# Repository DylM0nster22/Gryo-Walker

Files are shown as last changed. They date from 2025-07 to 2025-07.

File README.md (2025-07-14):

# Torque Walker
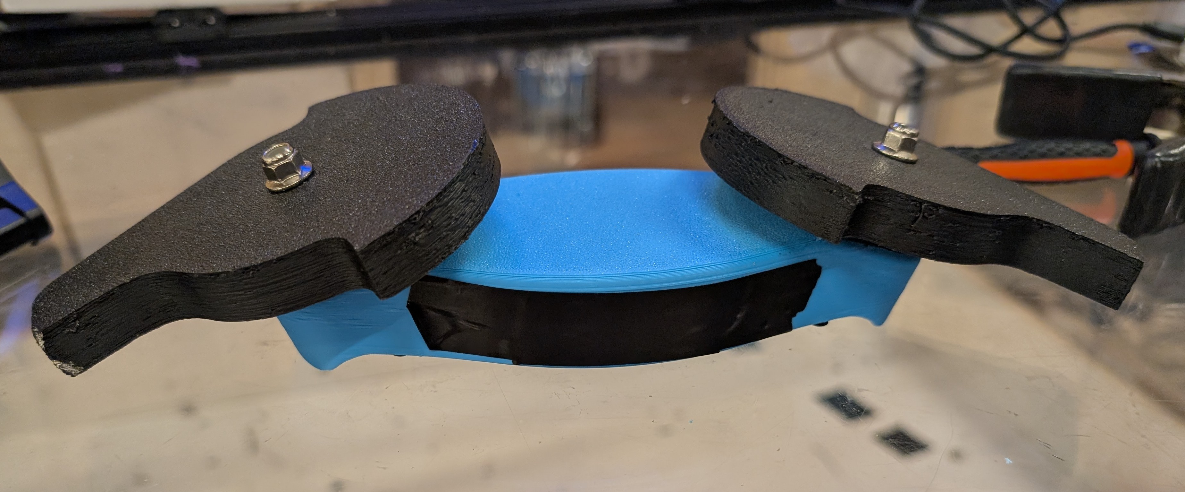
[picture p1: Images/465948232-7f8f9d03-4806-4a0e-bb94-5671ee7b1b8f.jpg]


# [DEMO VIDEO](https://photos.app.goo.gl/9bNn2mUH8ifmHqGP9)

## Background

For our project for Undercity, we made a torque walker combat robot. This style of robot has two diagonally spinning blades, with one on each side of the robot. The blades rotate in opposite directions. By adjusting the speed of each blade, the torque reaction causes the robot to pivot, which can be used to create a walking motion. 

The blades and frame were all printed from PLA. The robot has two RS2205 motors, one per weapon, which are held on with M3 x 8mm screws. These motors are drived by LanRC 35A ESCs, which are in turn powered by a 300mah Gaoneng LiHV 3S battery. The robot is powered on and off thorugh a fingertech switch, with the switch located in the bottom of the robot. We used a Malenki HV as our receiver, as it is what we had on hand. All of the electronics are held in by the bottom plate, which was held on with 4 M3 plastites. 

## Features

* Two large 5" diameter asymmetric disk weapons
* Tip speed exceeding 300 mph
* 3S 300mah High Voltage LiPo
* Able to be built with only off the shelf parts and 3D prints.

## Images

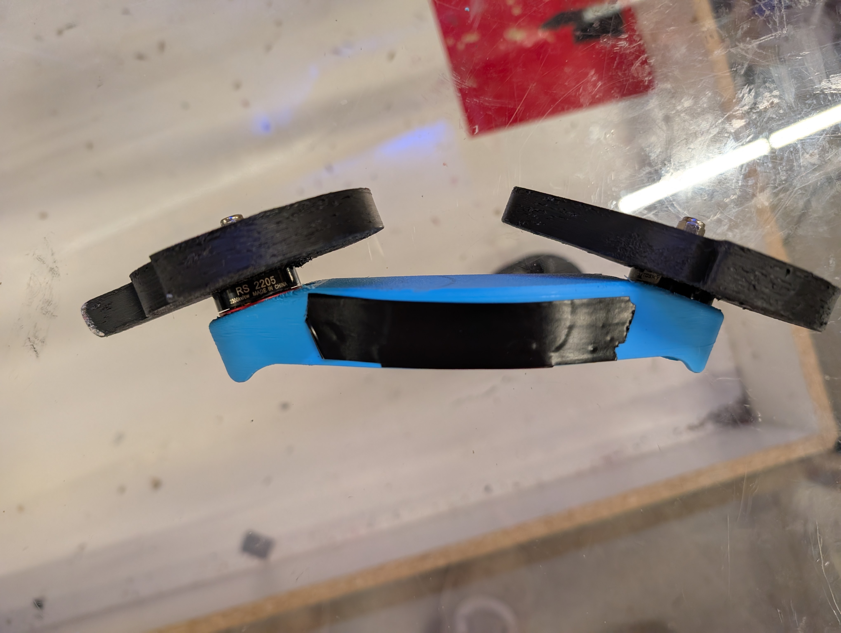
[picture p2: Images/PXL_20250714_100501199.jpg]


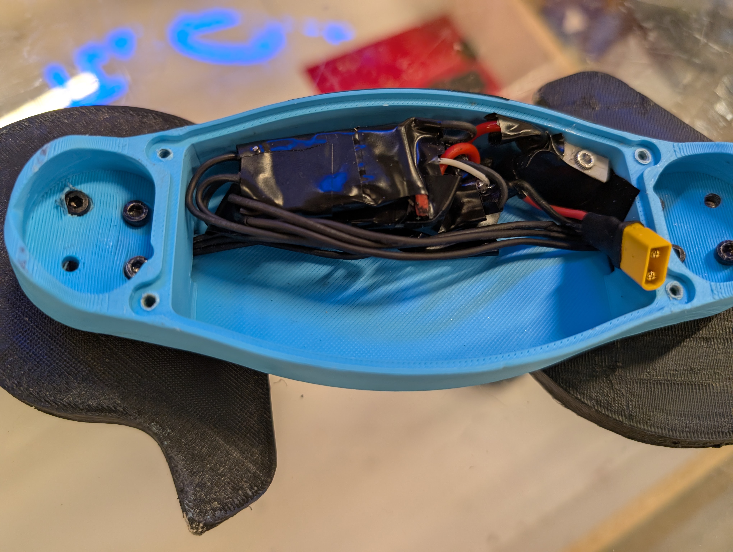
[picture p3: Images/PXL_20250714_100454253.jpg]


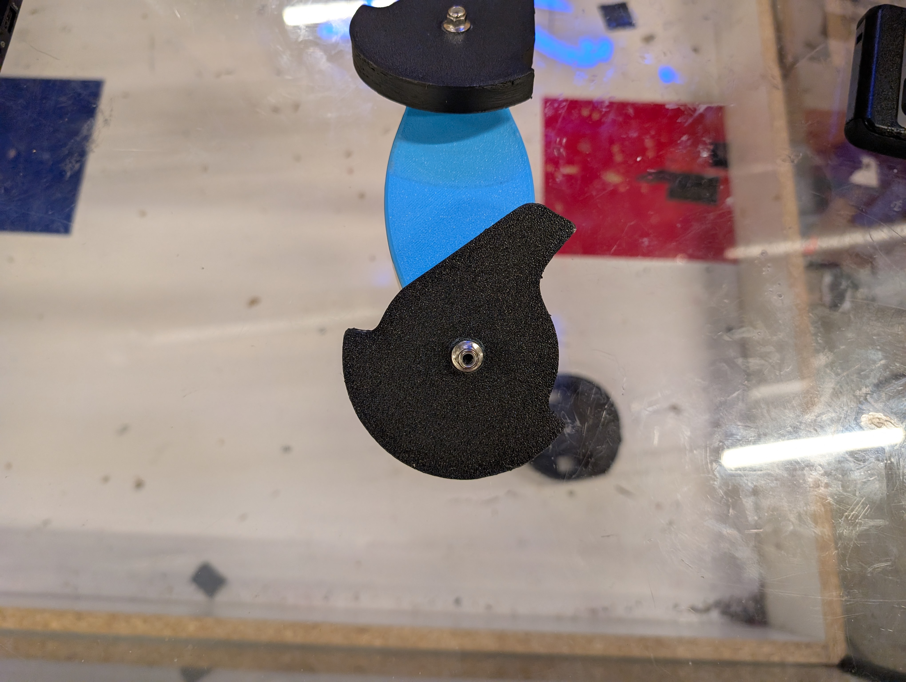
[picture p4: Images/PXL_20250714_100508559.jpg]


## Build Process

### Printing

**IT IS VERY IMPORTANT THAT WHEN PRINTING THE WEAPONS, ONE OF THE WEAPONS NEEDS TO BE MIRRORED.**

To begin the build process, first print all of the parts out of PLA. The robot is compact enough to be underweight for the plastic antweight class with almost any print settings, but the recommended settings are at least 4 walls 15% infil for the frame and all top layers (solid) for the weapons. This ensures that the robot is capable of holding up to the forces of combat.

### Electrical

The first step in the electrical system is to take a male XT30 and solder a black wire onto the negative side, and a red wire to the positive side (matching the battey). Solder the negative wire onto the negative terminal of the Malenki, and the positive wire onto one of the switch's tabs. Then solder another red wire onto the other tab of the switch, and then the other side of the wire can then be soldered onto the Malenki's positive terminal. 

Next, solder white signal wires onto each of the Malenki's weapon channel signal pads. Each signal wire can then be soldered onto an ESC. To power the ESCs, daisychain off of the Malenki's power pads to one ESC, and then from that ESC to the next. 

Put the Malenki, switch, and ESCs inside the robot and have the motors outside the robot, with the phase wires running through their slots. The three phase wires from each motor can then be soldered onto each ESC's three phase wire pads. 

Make sure to wrap everything in electrical tape to prevent any shorts.

Here is a wiring diagram for assistance:

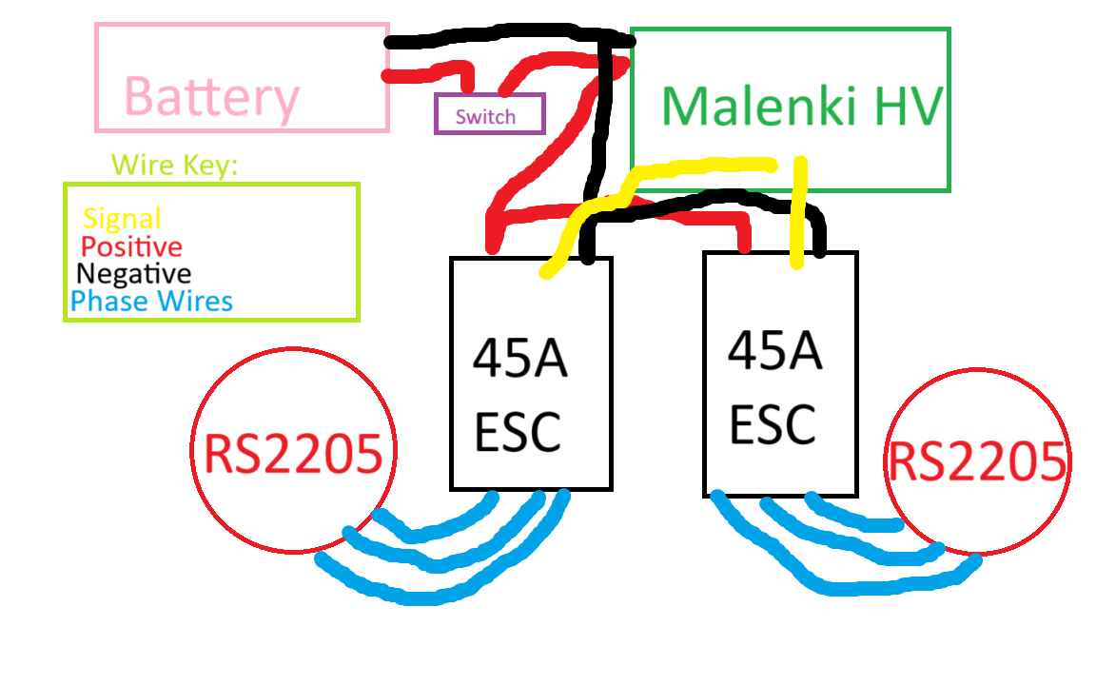
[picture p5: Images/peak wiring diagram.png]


### Assembly

The first step in assembling the robot is supergluing the switch into a corner. Pay attention to roughly where in the corner the switch hole is located on the top plate. However, it does not matter which corner, as the top plate can be flipped to line up properly. Depending on how the switch lines up, you may need to expand the hole on the top plate. This can be done by twisting flush cutters on the hole.

The motors can now be attached using four M3 x 8mm screws on each motor. Be careful not to use screws that are too long, as they can damage the motor's windings and cause a short. 

The weapons are attached by pressing them onto the motor can and putting a nut on the end of the shaft to hold them on. Depending on how the weapon press fits onto the can, it may need to be reprinted with different horizontal expansion settings or adjusted with a soldering iron or dremel. Loctite should be used on the nut to ensure that the vibrations do not cause them to back off. 

At this point, the battery can be inserted into the robot, and the bottom plate can be screwed on with four M3 plastites. 

Your robot is now ready for combat!

## Bill of Materials

|Name |Quantity|Price |Link |
|---|---|---|---|
|3S 300mah LiHV battery|1 |9.99  |https://share.google/nfxOtIxxwKT0yrfrc |
|Malenki HV |1 |46 |https://share.google/stp66j1LGnYxclgG8 |
|Fingertech Switch |1 |7.99  |https://share.google/lWe0jieE8vX2Iteq6 |
|45A Drone ESC |2 |39.6  |https://a.co/d/7bp3fm2 |
|RS2205 |2 |14.62 |https://share.google/J0T66sHt1AGzdSqSs |
|M3 x 8mm Screw |8 |5.99  |https://a.co/d/7sxAajj |
|M3 Plastite |4 |12.16 |https://www.mcmaster.com/product/96817A323|
|PLA Filament |~250g |5.99  |https://a.co/d/7vjEASh |
|XT30 |1 |1.99  |https://share.google/1hgPaIf5fwCM2d9de |
|Total: |N/A |144.33|N/A |

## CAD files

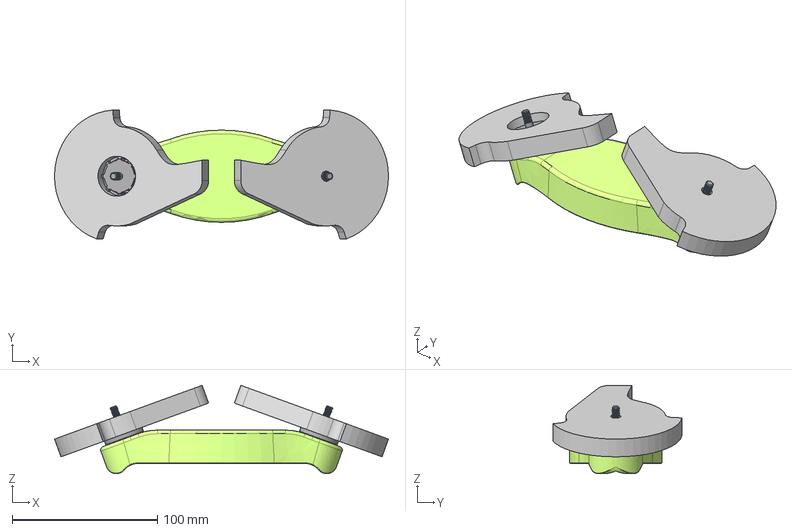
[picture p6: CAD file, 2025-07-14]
Full CAD.step
229.9 x 88.7 x 60.8 mm
Bottom Plate
Weapon 1
Weapon 2

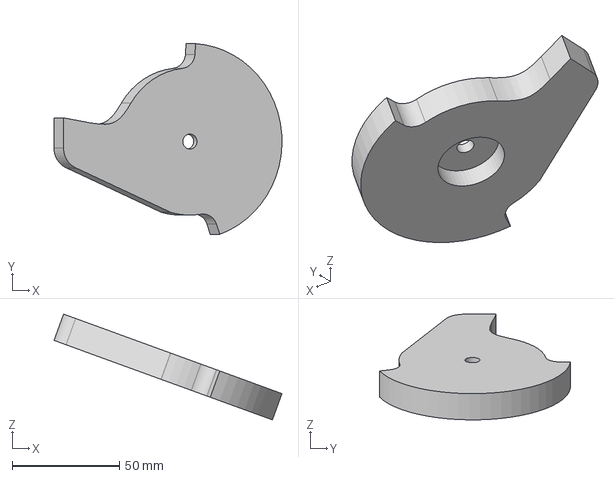
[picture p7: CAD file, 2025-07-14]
Individual Part STLs/Weapon.step
106.1 x 88.7 x 49.2 mm

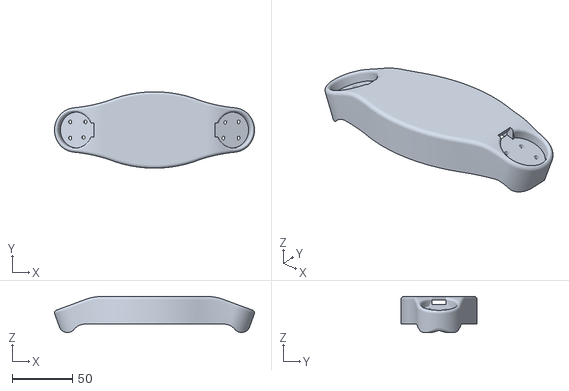
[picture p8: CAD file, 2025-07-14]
Individual Part STLs/Body.stl
166.3 x 63.5 x 30.0

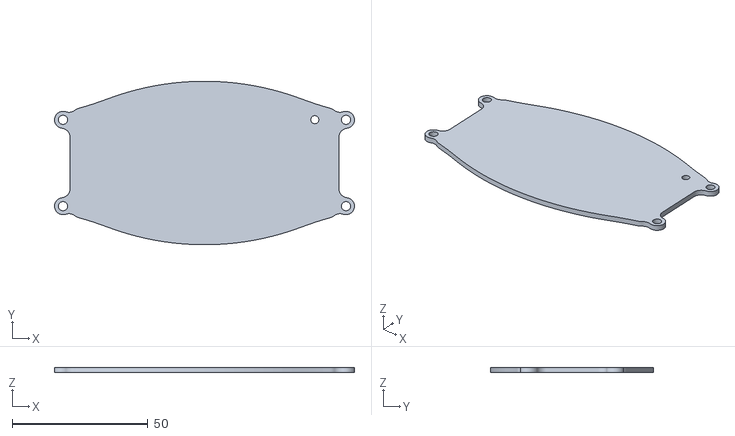
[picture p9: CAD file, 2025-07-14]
Individual Part STLs/Lid.stl
110.6 x 60.3 x 2.00

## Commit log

2025-07-14 Update and rename Torque Walker.step to Full CAD.step
    [Full CAD.step]
2025-07-14 Rename Lid.stl to Individual Part STLs/Lid.stl
    [Lid.stl]
2025-07-14 Update and rename undercity weapon.step to Weapon.step
    [Weapon.step]
